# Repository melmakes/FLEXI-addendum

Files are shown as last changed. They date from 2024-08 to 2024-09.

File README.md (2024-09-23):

# FLEXI Hardware Construction

Hello there! Now, this may be fairly non-standard, but I'm here to explain to you how to build your own **FLEXI (any pronouns)**! The [original paper](https://osf.io/dbg6h/) on FLEXI is wonderful, but flawed. And in attempting to construct a FLEXI for the Robot Studio, this became clear to me. My name's Melodie Jaeger (she/they) and I will be guiding you through everything that was overlooked in the hustle and bustle that can come with trying to meet paper submission deadlines. 

In this document, I will be going over a few key topics that are necessary in order for you to construct your very own FLEXI. The instance of FLEXI that I built ended up being named **Violet (she/her)** and I will be using that designation to delineate between her and FLEXI as a wider designation for the project. The original paper neglected a few details here and there, and while I had access to Dr. Alves-Oliveira and her files on the project, not everybody does, so an addendum became necessary. As well, this addendum will serve as a gallery of photos of **Violet**, for reference on what FLEXI **should** look like, approximately. Outside of this introduction, I'll try to avoid unnecessary fluff as much as possible. Without further adieu, let's get into it!

## BoM Addendum 

First up, the BOM! I've included a list of everything that was excluded from the original BoM that is necessary for basic functioning of FLEXI, in the file `bom_addendum.csv`.

Not included in this mini-BoM is zipties, which I think are pretty common
for labs to have, and aren’t *necessary*, but will help you with cable management. A solder station and a bit of heat-shrink wouldn't hurt, either.

Oh, and make sure the USB-A to USB-C cable is right angle or 180 degree on the USB-C end. This is necessary for proper fitting of the faceplate over the Pixel.

## Aluminum Parts Fabrication

Next, since most of the structural parts of FLEXI are made of cut aluminum, I'm including some guidance on that. I can't tell you how to work whatever equipment is available to you, but I can advise on buying the material and laying it all out. 

A note for buying the stock, I was able to make an 8" by 8" sheet of .190" thick aluminum work for the largest part, `circular_base.dxf`. If you're not deeply confident in your ability to set up your cutting equipment with precision, you probably want to get a larger sheet, as this part has a diameter of 200 mm, allowing for only 3 mm of tolerance (8" = 203 mm). For purchasing the materials, I've included a little table of what to get, in the file `alu_stock.csv`.

I've included all the DXF files you should need if you buy the aluminum stock as outlined in `alu_stock.csv`, and placed them in the `cut_files` directory. The spreadsheet with the stock says which files to use for what.

If you want to do the nesting yourself (maybe you already have an appropriate sheet of aluminum with weird shapes of free space?), the [OSF](https://osf.io/dbg6h/) repo contains the .dxf files for cutting all the parts for FLEXI, and then you can use a nesting software, such as [Deepnest](https://deepnest.io/) to arrange the parts on your stock sheets. 

## Faceplate 

The faceplate is a rather simple piece, made of a 3D printed part, `faceplate.stl`, and 2 M2.5 threaded heat-set inserts. I chose to paint the one on **Violet** a lovely lilac shade. This, in general, is one of the easiest parts to base little customizations and fun details around.

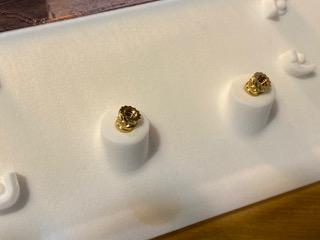
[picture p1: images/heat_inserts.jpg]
an image of two heat-set inserts on FLEXI's faceplate just before they were heated


## Construction

Another goal of this document is to supplement the original instructions for building FLEXI. In building **Violet**, I had a lot of trouble with these instructions, especially since it looks like they tried to fit the entire process on one page, with varying results. There are also simply a few typos and mistakes that I'd like to save you some time with. Concerning the directions on page 1185 of the original paper:

- There is no direction on what fasteners to use for what. Use your best guess/intuition for this, and for most parts of the construction, it'll be fine. The kits in the BoM have plenty of nuts and bolts.
- Step 1 is very unclear about standoffs and spacers. I used M3 x 8 standoffs to attach the makerbeams to the part labelled "square base". I used a stack of washers for the parts labelled simply "spacers". Alternatively, for this step, you can use M3 screws and spacers, but the holes are sized for M4. It's probably fine either way.
- In Step 2, the motor labelled "Dynamixel motor" is the XH540-W270-T motor called for in the BoM.
- In Step 3, I would advise not attaching the phone plate just yet. What you should do is attach the phone case to the phone plate, using the faceplate as a jig to make sure everything fits together properly. 

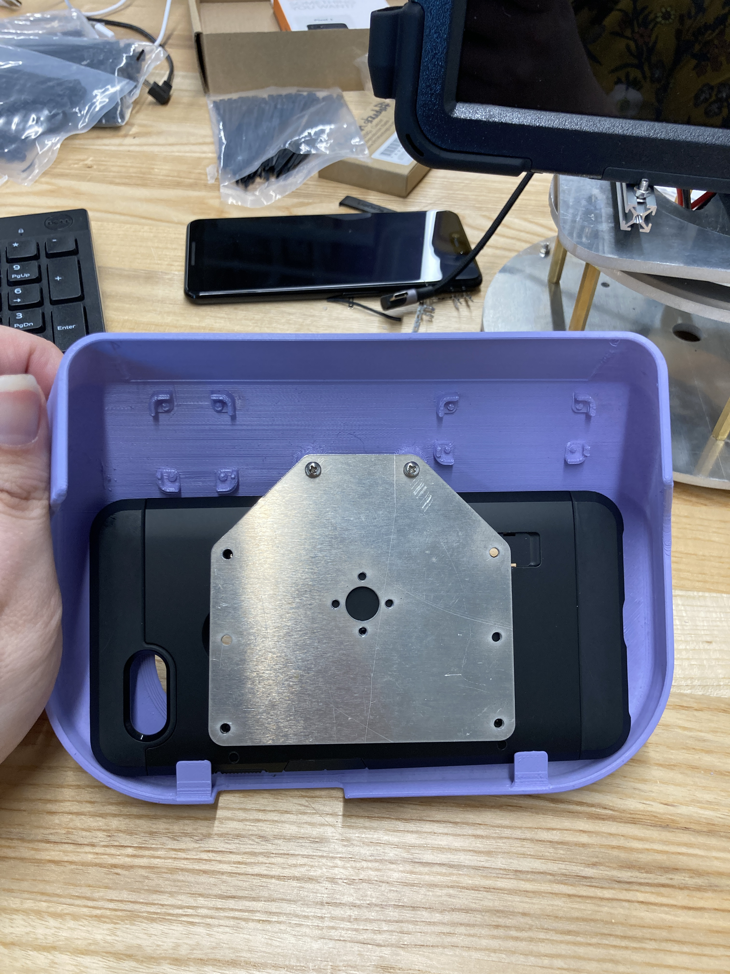
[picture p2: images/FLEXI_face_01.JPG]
an image of the phone plate, Google Pixel case, and faceplate assembled in the above-mentioned jig
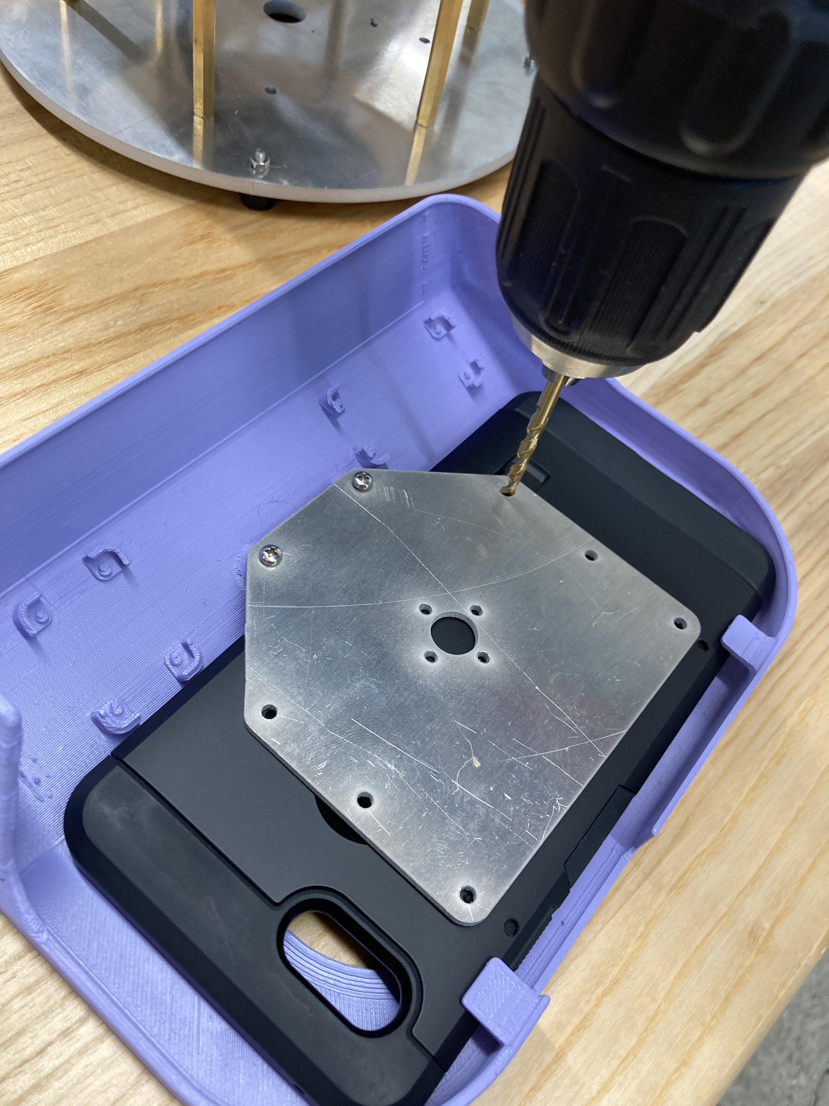
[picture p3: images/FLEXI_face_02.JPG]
an image of the phone case being drilled with M2 holes


- For securing the phone case to the phone plate, use the M2 screws and some M2 nuts. I used 4, as shown here:

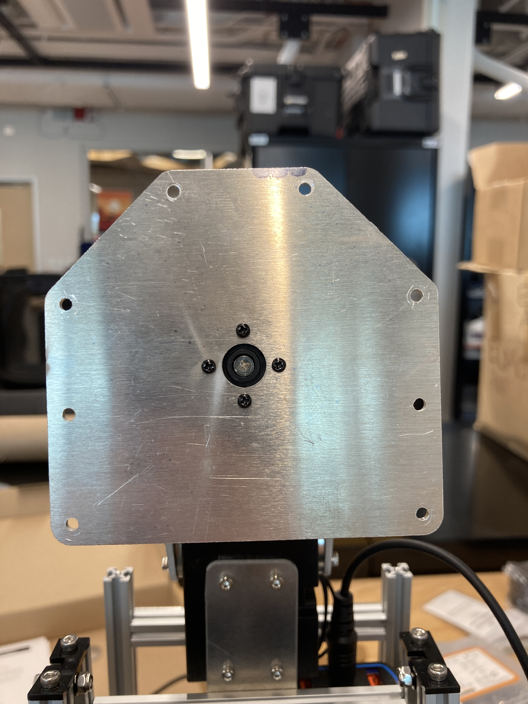
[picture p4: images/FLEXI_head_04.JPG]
an image of the phone plate secured to the upper neck motor
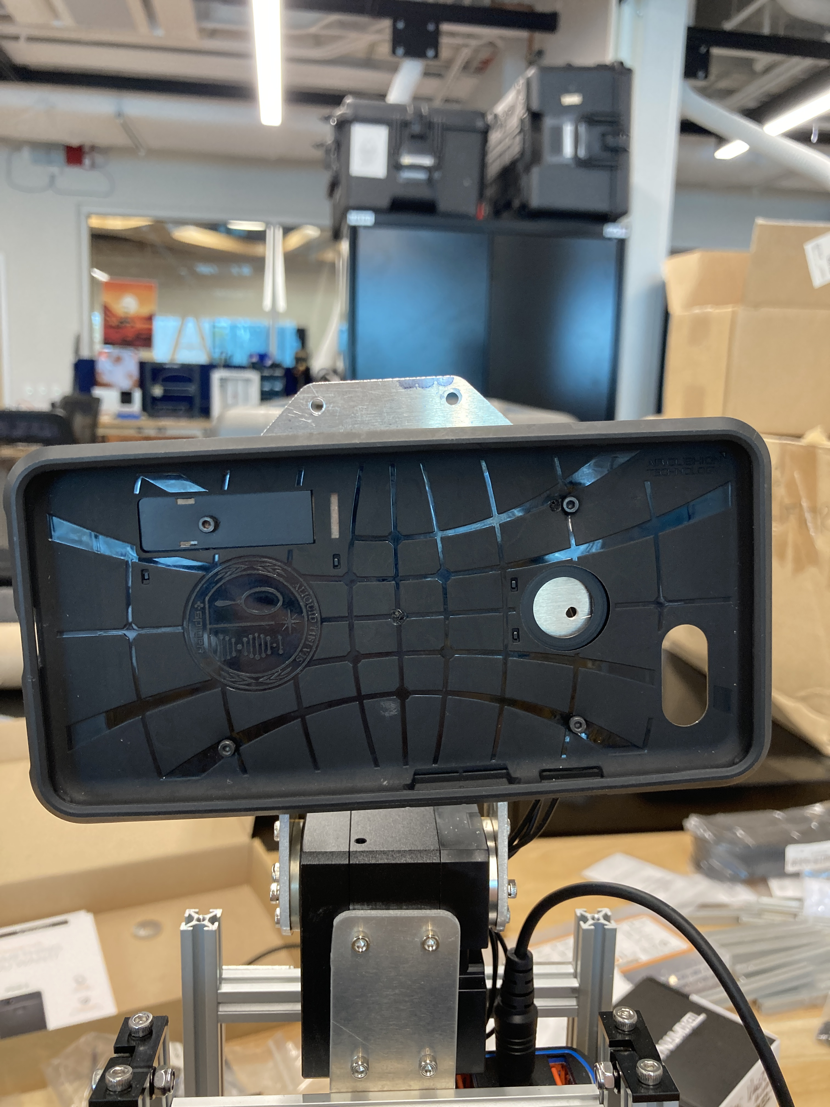
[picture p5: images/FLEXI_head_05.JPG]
the phone case screwed into the phone plate
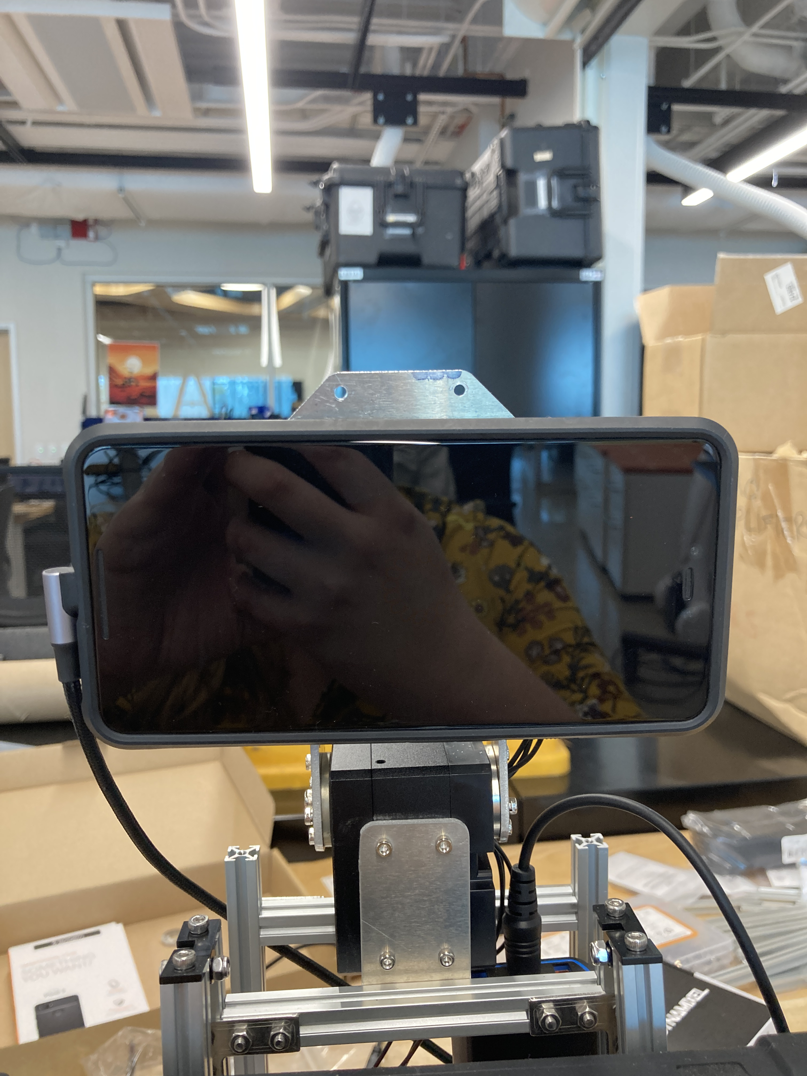
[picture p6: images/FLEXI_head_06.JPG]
the Pixel inserted into said case
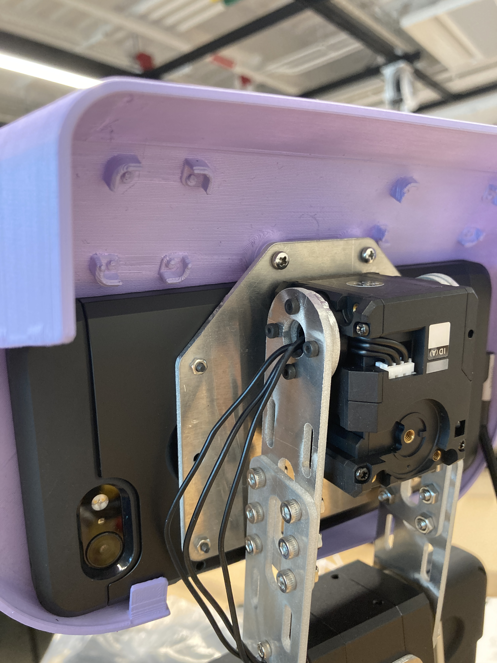
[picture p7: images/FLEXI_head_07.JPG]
faceplate screwed onto phone plate
    

- Also, in Step 3, the motor labelled as "Motor B" is the 2XC430-W250-T, and each of the two axes connected by the neck parts requires an idler. Look in the manuals for the idlers in the BoM to see which motors they correspond to. 
- Oh, and in Step 3, the part labelled "150MM Makerbeam" is, in fact, supposed to be a 100mm Makerbeam. Save yourself the headache of disassembly and reassembly.
- Step 4 is a bit tricky, so I've included an image that should help guide you through it: 
 
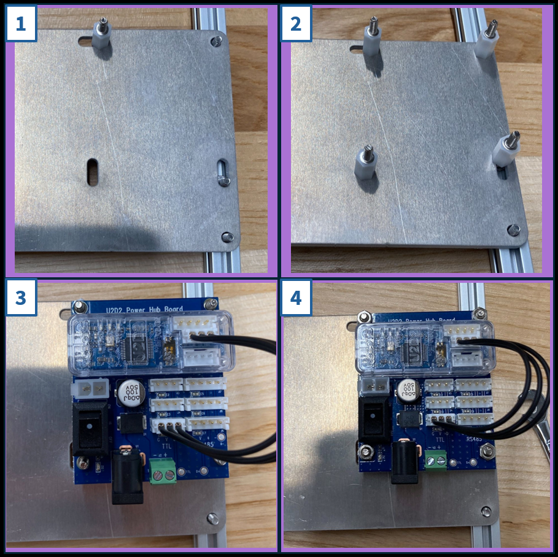
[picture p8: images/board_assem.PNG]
step by step assembly for the control board


The remainder of the original instructions for building FLEXI are pretty simple and easy to follow, aside from the wiring. And it's my hope that some of the images I've included (in the `images` folder) can help.

## Wiring

The wiring documentation in the original paper is... lacking. I'm not convinced that this isn't a strange choice, but you may have noticed that it calls for a car charger for the Surface Pro, and then that is wired into a barrel plug in parallel with the U2D2. If there is future work on the desin of FLEXI, this is the most obvious place to start. I feel like a well-designed and very minimal PCB could handle some of this shall we say... jank.

 **Note**, by the way, that the U2D2 is wired differently for FLEXI than what the U2D2 [e-manual](https://emanual.robotis.com/docs/en/parts/interface/u2d2/) says. Otherwise, I found that the manuals from Robotis for the motors and U2D2 were very helpful.

The wiring on FLEXI truly isn't all that complex. In putting the thing together myself, I elected to forego the crimp connectors in the BoM for some good ol' fashioned splicing with heat-shrink and solder. If you don't know how to splice wires, you can find a ton of great online guides. Follow the wiring diagram included with the original paper, and use the barrel connector included in `bom_addendum.csv`. Here's a few images of the finished wires for the power:

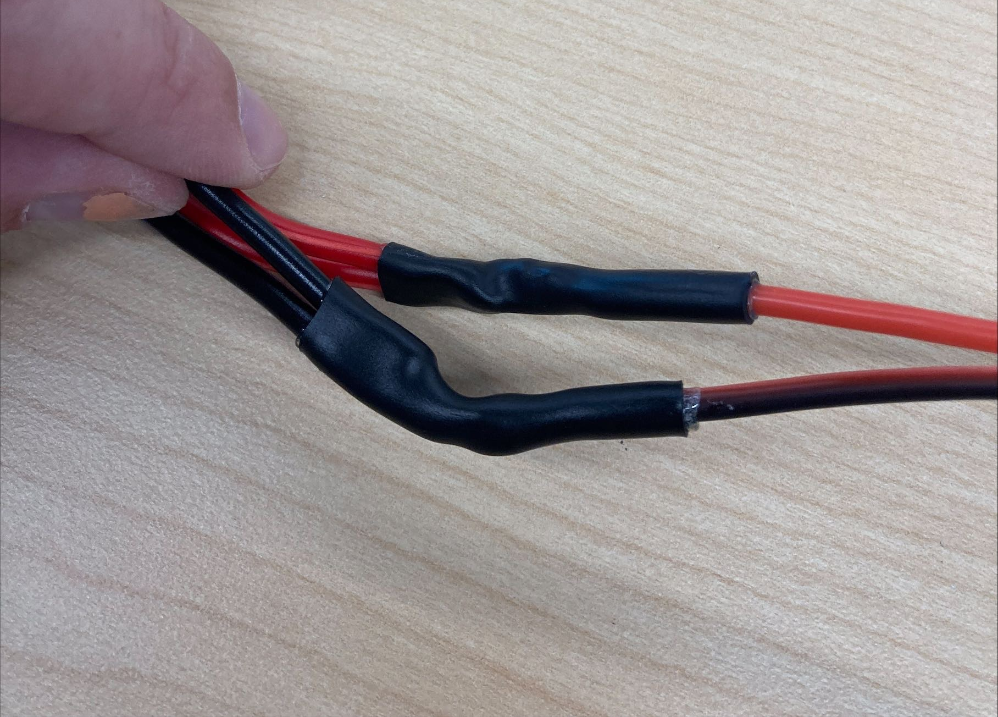
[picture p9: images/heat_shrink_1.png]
an image showing the end result of the wire splicing process

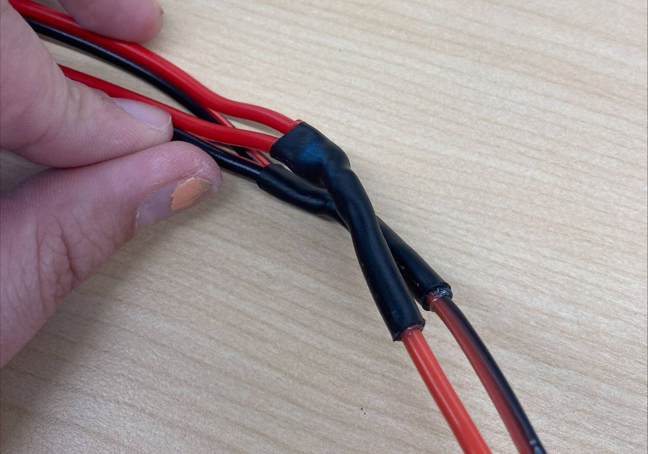
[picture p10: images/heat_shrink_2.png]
an alternate perspective on the above image

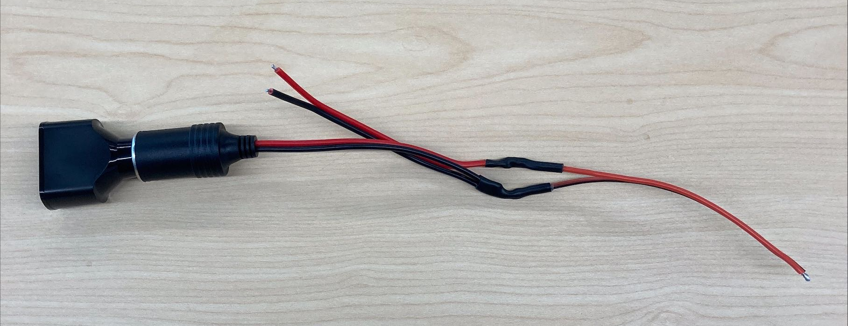
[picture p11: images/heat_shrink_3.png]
an image of the completed power supply wiring, prior to insertion into the robot


In addition, there is a lot of wiring involved in making all of the connectivity that FLEXI needs to function. Some of the cables needed for this can be found in `bom_addendum.csv`, but basically, you just need to be able to pass a lot of data between the Surface, the Pixel, and the U2D2. Here's a wiring diagram that I found useful, but did not create. It was buried in the old google drive folder for this project:

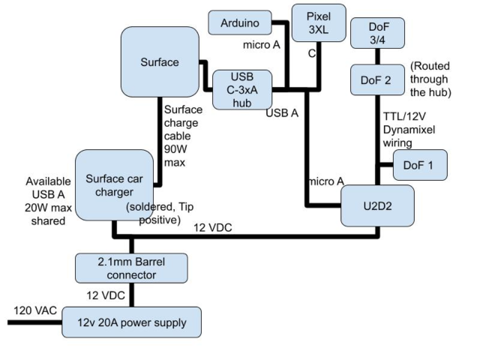
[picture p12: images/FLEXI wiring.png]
FLEXI wiring diagram


## Gallery

I had a lot of images of FLEXI, and felt that pretty much all of them would be good to include. So, I'm basically just going to dump a bunch of photos in the `images` folder for reference.

## Future Work

So, I'm no longer working under Patricia, meaning that my time working on FLEXI is most likely at an end. But, were I to make some changes to FLEXI, I do have a few ideas:

### A Power Supply PCB Design

As I mentioned above, there are some problems with the electronics. The number one thing I'd like to see improved is a change to this car charger-based design. I can't imagine that creating a PCB design that accomplishes everything the car charger is used for would be too difficult, especially for an electrical engineer seasoned in PCB design.

### A Unified Documentation for the Software

The software for FLEXI is a bit disorganized. For its visual design, it implements [FLEX-SDK](https://dl.acm.org/doi/abs/10.1145/3526113.3545707) (link to [repo](https://github.com/mayacakmak/emarsoftware/wiki)), but you won't find a repository for the motor control online. I had access to some old Google Drive folders from the original project, and I still couldn't get it to work. Given a bit more time, getting **Violet** fully functioning was my goal, and this was an obstacle to that goal.

### A Stand-Alone Design

FLEXI uses a Google Pixel and a Microsoft Surface Pro. These aren't the most expensive bits (those would be the motors), but they do contribute to a large percentage of the budget for this project. It seems to me that rather than a browser-based system that also relies on running Python code for motor control via Windows, something more inspired by [Tulip](https://tulip.computer/) or [norns shield](https://monome.org/docs/norns/shield/) might be a better fit. (pardon my open source musician tendencies coming out)

What I mean is, something with:
- cheap hardware, based on something like the Tulip creative computer's touch screen display
- dedicated firmware, as opposed to this mess of poorly organized code. The kind of thing where you load the firmware on it, and it just *works*.
- and a system for making changes easily. Something running a barebones Linux OS would be perfect for this. FLEX-SDK attempts this, but feels like it needs a lot of polish. I'd personally be inclined to go with something like [maiden](https://monome.org/docs/norns/maiden/), the "app store" for norns.

## Acknowledgements

So obviously, I must thank [Dr. Patricia Alves-Oliveira](https://patricialvesoliveira.com/) for giving me the opportunity to work on this project. It was a lot of fun, as well as being a valuable experience.

I also need to make a shoutout to [Skye Krzykwa](https://linktr.ee/krzyksky), who helped me with some of the electrical stuff. I came into this project with very little knowledge of electronics, and she might feel like she barely even helped, but I couldn't have built **Violet** without the help she provided.

And finally, I'd like to thank the original design team for FLEXI! I may have some critiques of their work, but learning from our mistakes is how we advance towards better things, and learning from others' mistakes is kinda one of the best things about this whole open-source community!

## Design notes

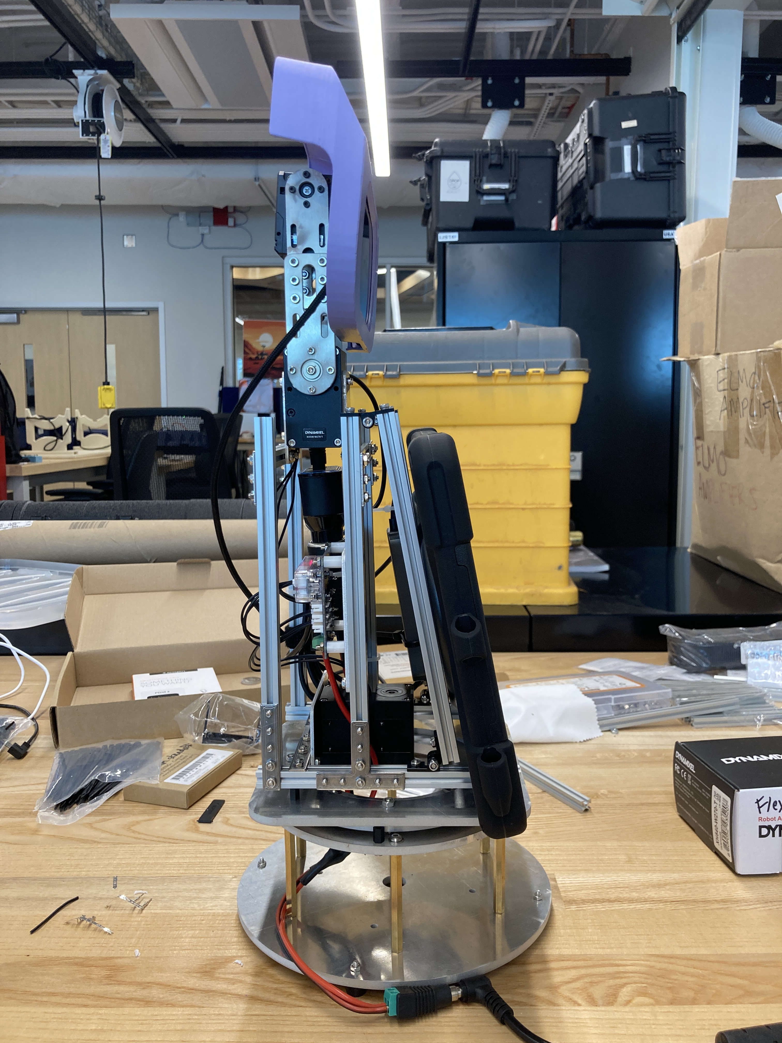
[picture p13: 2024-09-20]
images/FLEXI_pano_05.JPG

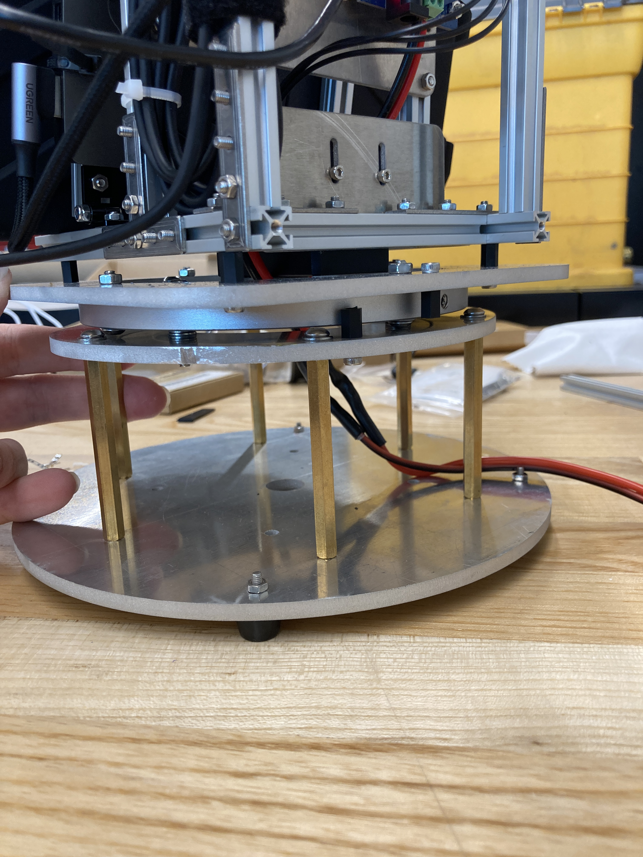
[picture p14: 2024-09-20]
images/FLEXI_base_02.JPG

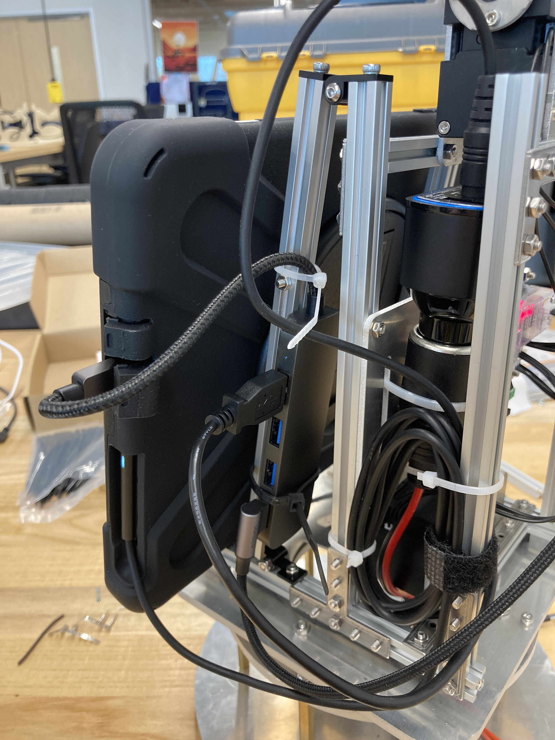
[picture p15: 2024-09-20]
images/FLEXI_wires_02.JPG

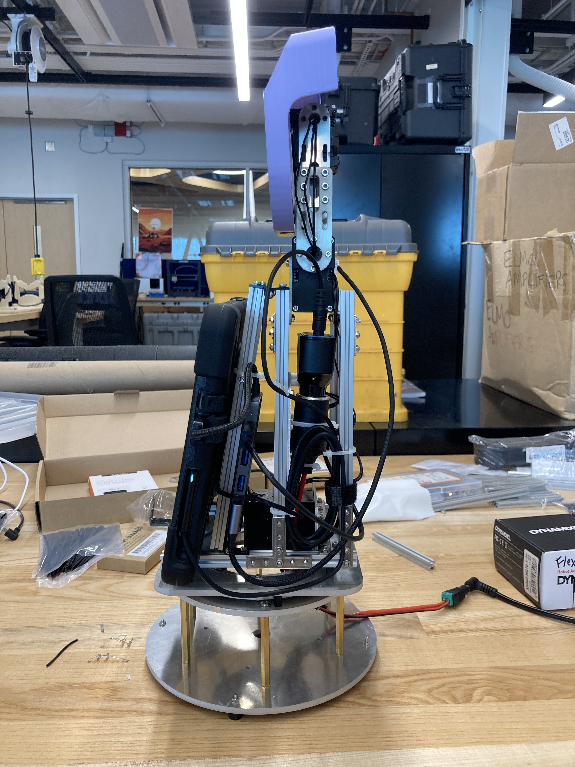
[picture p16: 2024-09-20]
images/FLEXI_pano_01.JPG

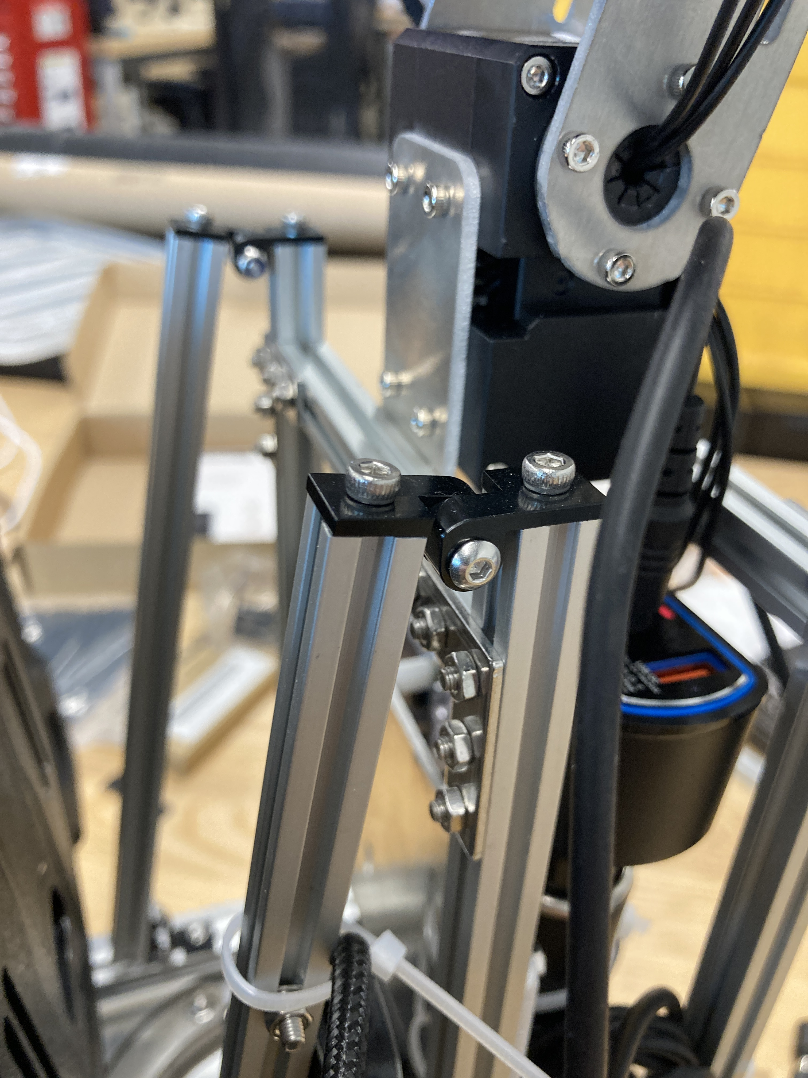
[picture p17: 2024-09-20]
images/FLEXI_misc_01.JPG

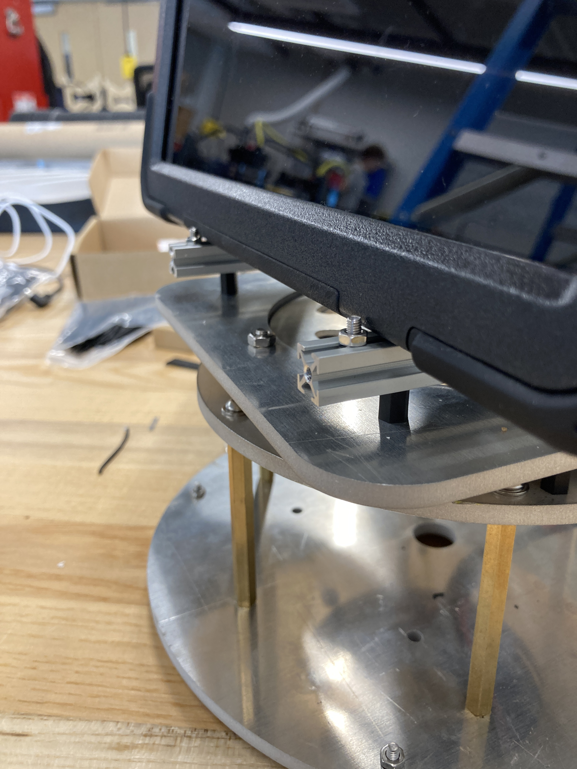
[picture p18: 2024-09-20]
images/FLEXI_misc_02.JPG

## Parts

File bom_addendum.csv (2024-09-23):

Designator | QTY | Cost (USD) | Source | Info
Lazy Susan | 1 | <20 | *amazon link* | Necessary for smooth "waist" motion
M2.5 x 6mm Bolts, pack of 50 | 1 | $11.56 | https://www.mcmaster.com/91290A101/ | to fasten faceplate to phone plate
M2.5 Threaded Heat-Set Inserts, pack of 100 | 1 | $17.56 | https://www.mcmaster.com/94180A321/ | to fasten faceplate to phone plate
Zipties | 10-15 | <$20 | https://www.mcmaster.com/products/zip-ties/cable-ties-2~/cable-ties-7/ | for cable management. Smallest pack looks to be 25, more than enough
M4 x 3mm spacers | 4 | $1.62 | https://www.mcmaster.com/93657A004/ | Use these in Step 1, labelled "spacers"
USB Hub | 1 | $47.02 | https://www.digikey.com/en/products/detail/startech-com/HB30C4AIB/21398321 | to connect Surface to U2D2, Arduino, and Pixel
USB A->Micro Cable | 2 | $2.65 | https://www.digikey.com/en/products/detail/qualtek/3025033-01/6235029 | to connect USB Hub to U2D2 and Arduino
USB A->C Right Angle Cable | 1 | $3.95 | https://www.digikey.com/en/products/detail/adafruit-industries-llc/5031/14625566 | to connect USB Hub to Pixel, needs to be right angle at USB C end to fit faceplate
Female Barrel Connector with Terminal Block | 1 | $1.00 | https://www.digikey.com/en/products/detail/led-lighting-inc/FB-CON/12687320 | to connect spliced power circuit to power supply
12VDC, 10A Power Supply | 1 | $50.60 | https://www.digikey.com/en/products/detail/tt-electronics-power-partners-inc/PEAMD120-12-B2/15838890 | to connect barrel connector to wall plug, and power FLEXI
1/2" Inner Diameter Heat Shrink, Feet | 1 | $3.45 | https://www.digikey.com/en/products/detail/te-connectivity-raychem-cable-protection/NTFR-1-2-0-SP/5317866 | for splicing power supply wires

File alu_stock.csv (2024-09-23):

Component | Quantity | Price | Link | Description
8" x 8" sheet, 0.190" thick | 3 | $19.07 | https://www.mcmaster.com/89015K279/ | For 1x base-ring, 1x circular-base, and 1x outer-ring. These cuts are large enough that they could not be nested.
12"x 12" sheet, 0.100" thick | 1 | $23.20 | https://www.mcmaster.com/89015K961/ | For 2x neck-bracket-distal, 2x neck-bracket-proximal, 4x neck-bracket-spacer, and 1x mounting-plate. These are nested in the file nested_drawing_100.dxf
8" x 8" sheet, 0.080" thick | 1 | $9.57 | https://www.mcmaster.com/89015K196/ | For 2x neck-motor-plate, 1x phone-plate, 1x slew-motor-bracket, and 1x torque-tongue-lazy. These are nested in the file nested_drawing_080.dxf

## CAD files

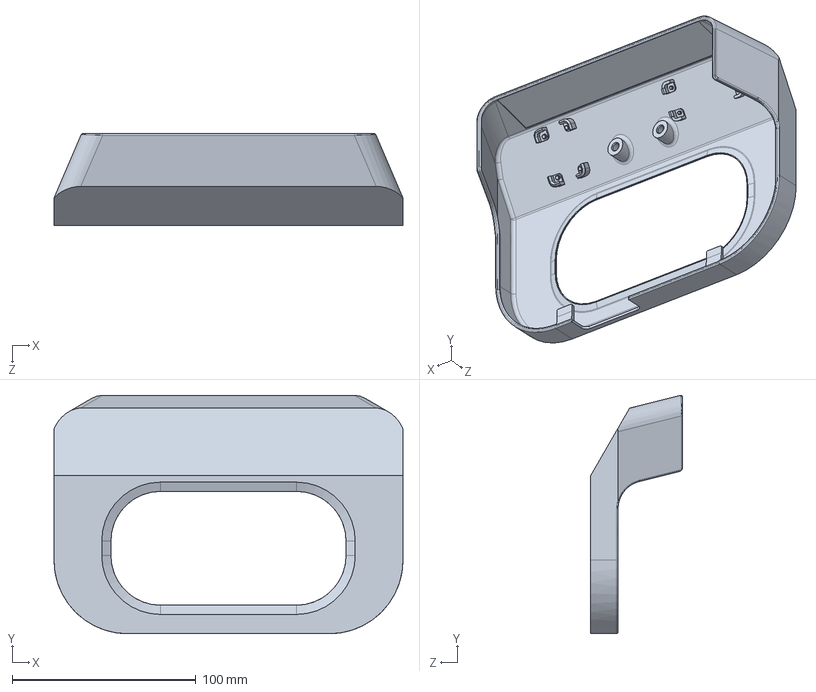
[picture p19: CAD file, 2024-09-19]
cad_files/faceplate.SLDPRT
190.0 x 129.8 x 50.0 mm

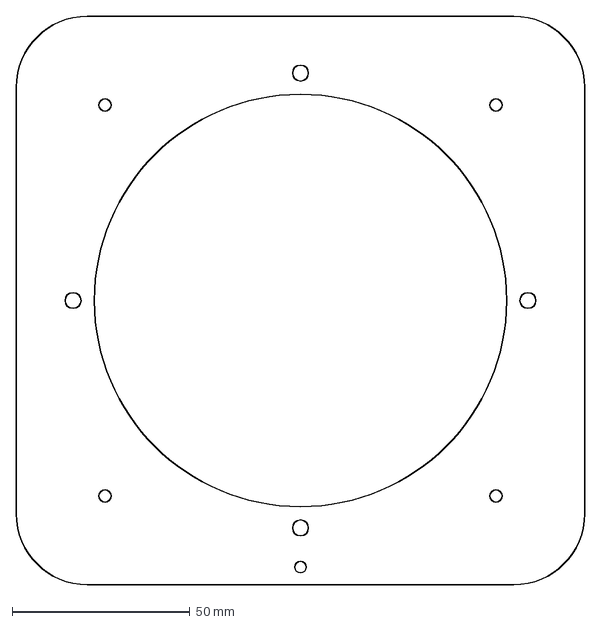
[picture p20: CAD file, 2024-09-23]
cut_files/outer-ring.DXF
160.0 x 160.0 mm

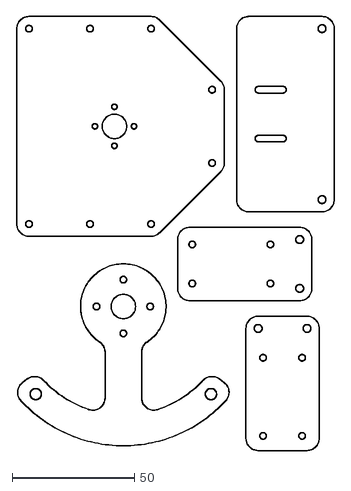
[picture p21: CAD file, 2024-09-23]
cut_files/nested_drawing_080.DXF
130.3 x 178.1

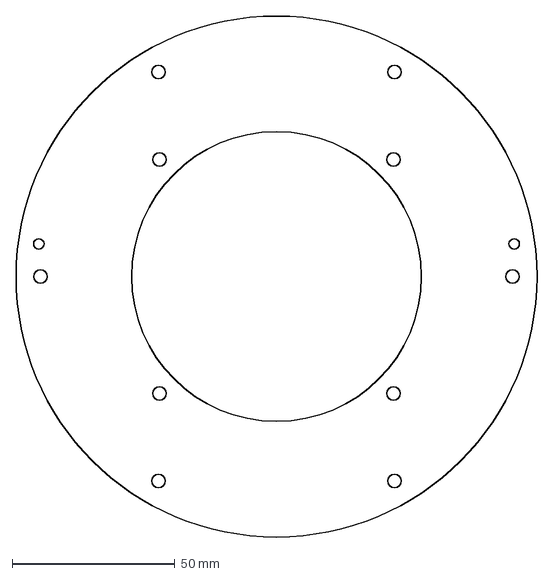
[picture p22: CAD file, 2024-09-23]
cut_files/base-ring.DXF
160.0 x 160.0 mm

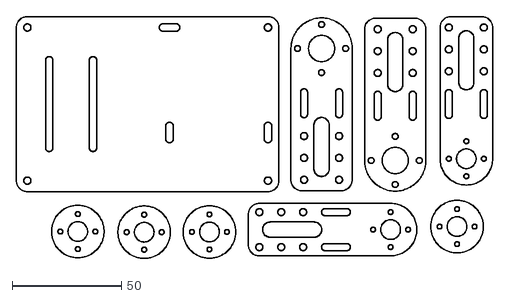
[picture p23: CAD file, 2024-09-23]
cut_files/nested_drawing_100.DXF
218.0 x 110.9

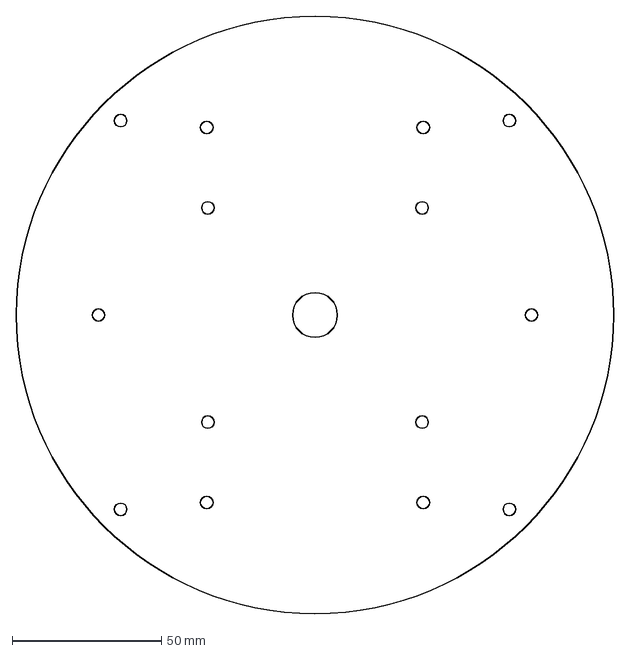
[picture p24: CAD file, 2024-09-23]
cut_files/circular-base.DXF
200.0 x 200.0 mm

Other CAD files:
cad_files/faceplate.STL

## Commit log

2024-09-05 finished construction, added to wiring
2024-09-19 inserting images in README
2024-09-19 adding images and cad files
    [faceplate.SLDPRT, faceplate.STL]
2024-09-23 bom addendum, missing one link
    [bom_addendum.csv]
2024-09-23 alu stock bom
    [alu_stock.csv]
2024-09-23 finishing up alu section
    [base-ring.DXF, circular-base.DXF, nested_drawing_080.DXF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]
